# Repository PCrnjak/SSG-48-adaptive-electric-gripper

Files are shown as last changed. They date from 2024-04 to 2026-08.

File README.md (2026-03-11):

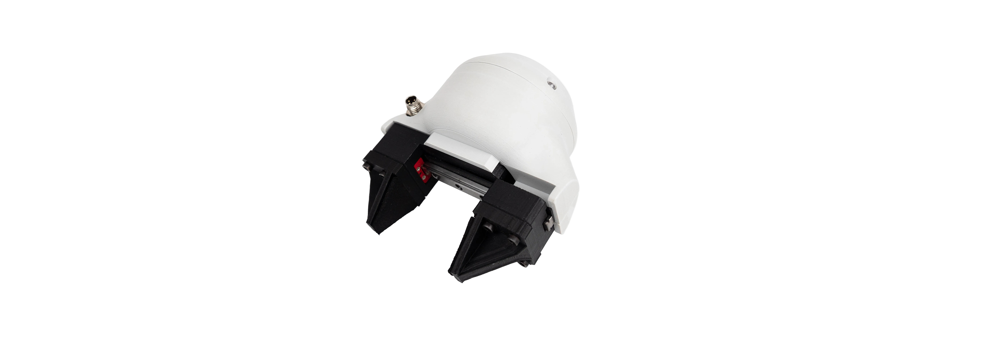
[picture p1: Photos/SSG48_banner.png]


<div align="center">

# SSG48 adaptive electric gripper
        

## [▶️YouTube🔴 Video of Gripper in Action!](https://www.youtube.com/shorts/DQgi8Ua-VAU)

</div>

## 📖 Project Overview

**SSG-48 adaptive electric gripper** is a gripper based on [Spectral micro BLDC drivers](https://source-robotics.com/products/spectral-micro-bldc-controller). It is a gripper capable of controlling its gripping force, making it perfect for assembly tasks and human-robot collaboration. Force can be adjusted from 5 N to 80 N allowing you to grasp a wide range of items; from delicate and soft to rigid and sturdy.

Mechanical files and firmware are open source allowing you to add a custom griping tool and attach it to any robotic arm or robot. Gripper software is also open-source. Gripper has a stroke of 48 mm and a mass of 400g.

## ⚒️How to build / Where to buy?

You can buy SSG48 adaptive electric gripper on our website: https://source-robotics.com/products/compliant-gripper

If you want to Source all the parts yourself and build your own follow these steps:

* Source all the parts from the [BOM](https://github.com/PCrnjak/SSG-48-adaptive-electric-gripper/tree/main/BOM)
* Follow [Assembly instructions](https://github.com/PCrnjak/SSG-48-adaptive-electric-gripper/tree/main/Assembly%20manual) or [Video instructions](https://www.youtube.com/watch?v=127zXHKuqIg) to assemble your gripper
* Follow [DOCS](https://source-robotics.github.io/SSG48-gripper-docs/page1_about_the_gripper/) to get your gripper up and running.

## 📚Documentation:

- [Product website](https://source-robotics.com/products/compliant-gripper)
- [GUI software](https://github.com/PCrnjak/SSG-gripper-GUI) 
- [Building instructions](https://github.com/PCrnjak/SSG-48-adaptive-electric-gripper/tree/main/Assembly%20manual)
- [BOM](https://github.com/PCrnjak/SSG-48-adaptive-electric-gripper/tree/main/BOM)
- [DOCS](https://source-robotics.github.io/SSG48-gripper-docs/page1_about_the_gripper/)
- [Python API](https://github.com/PCrnjak/Spectral-BLDC-Python/tree/main)
- [ROS2 package for SSG48 gripper](https://github.com/Lass6230/ssg48_adaptive_electric_gripper_ros2) /// [ROS2 package for MSG gripper](https://github.com/BiomechatronicsLab/source_robotics_msg_gripper_ros2)
- [URDF & MJCF files](/SSG48_gripper_description/)

## 💻Quick start code example

```python
import Spectral_BLDC as Spectral
import time

Communication1 = Spectral.CanCommunication(bustype='slcan', channel='COM20', bitrate=1000000)
Motor1 = Spectral.SpectralCAN(node_id=0, communication=Communication1)

Motor1.Send_Clear_Error()
Motor1.Send_gripper_calibrate()
time.sleep(4)

temp_var = 0
while True:
   if temp_var == 0:
      Motor1.Send_gripper_data_pack(50,100,700,1,1,0,0) 
      temp_var = 1
   elif temp_var == 1:
      Motor1.Send_gripper_data_pack(240,100,700,1,1,0,0) 
      temp_var = 0

   message, UnpackedMessageID = Communication1.receive_can_messages(timeout=0.2) 

   if message is not None:
      print(f"Message is: {message}")
      print(f"Node ID is : {UnpackedMessageID.node_id}")
      print(f"Message ID is: {UnpackedMessageID.command_id}")
      print(f"Error bit is: {UnpackedMessageID.error_bit}")
      print(f"Timestamp is: {message.timestamp}")

   time.sleep(3)
```

## 🌐 More about the SSG48 Adaptive Electric Gripper

| YouTube | Hackaday | Instagram | Twitter |
|---|---|---|---|
|  |  |  |  |

| Discord | Forum | Blog |
|---|---|---|
|  |  |  |

## ⚠️ Safety, Liability & Disclaimer
This project includes experimental software, hardware designs, and assembly documentation that are still under development and may contain bugs, errors, or incomplete features. By using, building, or modifying this project, you acknowledge that:

* You use this project entirely at your own risk
* You are solely responsible for safe assembly, testing, and operation
* No guarantee is made regarding correctness, safety, or reliability
* The authors are not responsible for any damage, injury, or loss resulting from the use or misuse of this project
* Hardware performance and safety depend on user assembly, component quality, calibration, and handling, which cannot be guaranteed
* This project is provided “as is.” If you choose to build a device yourself using these files, designs, or instructions, you do so without any warranties or guarantees, including regarding safety, reliability, or suitability for any particular purpose.

THIS PROJECT INVOLVES LETHAL VOLTAGES AND OTHER SERIOUS HAZARDS THAT CAN CAUSE SEVERE INJURY. YOU MUST READ THE FULL [SAFETY WARNING AND DISCLAIMER DOCUMENT](SAFETY_WARNING_AND_DISCLAIMER.md)  BEFORE USING ANY PROJECT FILES. BY PROCEEDING, YOU ACKNOWLEDGE AND ACCEPT ALL RISKS AND AGREE TO USE THIS PROJECT ENTIRELY AT YOUR OWN RESPONSIBILITY.

## 💸Support the project

The majority of this project is open source and freely available to everyone. Your assistance, whether through donations or advice, is highly valued. Thank you!

 


## 🛡️ Licensing
Project is under Apache 2.0 Licence

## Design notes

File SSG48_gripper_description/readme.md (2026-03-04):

# Source Robotics SSG48 gripper Description (MJCF)

> [!IMPORTANT]
> Requires MuJoCo 3.1.3 or later.

## Changelog

See [CHANGELOG.md](./CHANGELOG.md) for a full history of changes.

## ⚒️TODO 

- Add correct joint limits to URDF and MJCF files

## Overview

This package contains a simplified robot description (MJCF) and URDF files of the [SSG48 gripper](https://source-robotics.com/products/compliant-gripper) developed by [Source Robotics](https://source-robotics.com/).

## Jaw options

Folder contains few different jaw options for the gripper. You can change them by replacing the existing jaw options in the mesh folder by the ones you want.

## Online mujoco viewer

https://mujoco-viewer.org/

## URDF folder

[URDF](./URDF/) folder contains:
* SSG48 gripper
* Jaw options folder

More about URDF here: [Link](./urdf.md)

## URDF → MJCF derivation steps

1. Loaded the URDF into MuJoCo and saved a corresponding MJCF.
2. Manually edited the MJCF to extract common properties into the `<default>` section.
3. Added position-controlled actuators for the arm.
4. Added `scene.xml` which includes the robot, with a textured groundplane, skybox, and haze.

## License

This model is released under an [Apache-2.0 License](LICENSE).

## References

Mjcf reference Mujoco managerie
- references: 
- https://mujoco.readthedocs.io/en/stable/XMLreference.html
- https://github.com/google-deepmind/mujoco_menagerie/tree/main/ufactory_lite6
- https://github.com/google-deepmind/mujoco_menagerie/blob/main/trossen_vx300s/vx300s.xml 
- https://github.com/google-deepmind/mujoco_menagerie/blob/main/aloha/aloha.xml
- https://github.com/google-deepmind/mujoco_menagerie/blob/main/franka_emika_panda/panda.xml 
- https://github.com/jeongeun980906/lerobot-mujoco-tutorial/blob/master/asset/robotis_omy/omy.xml

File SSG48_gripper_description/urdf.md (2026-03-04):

Free online URDF viewers:
- https://gkjohnson.github.io/urdf-loaders/javascript/example/bundle/
- https://urdf.d-robotics.cc/
- https://viewer.robotsfan.com/

TO view any of the URDF arms drag the folder into the online viewer.

---

Great guide on how to generate URDF in solidworks: [Link](https://www.youtube.com/watch?v=I08lO_SRBbk)

---

How to convert URDF to MUJOCO file format: [Link](https://www.youtube.com/watch?v=v2OfmQaoIH4) 

Note add .\ before compile command on windows

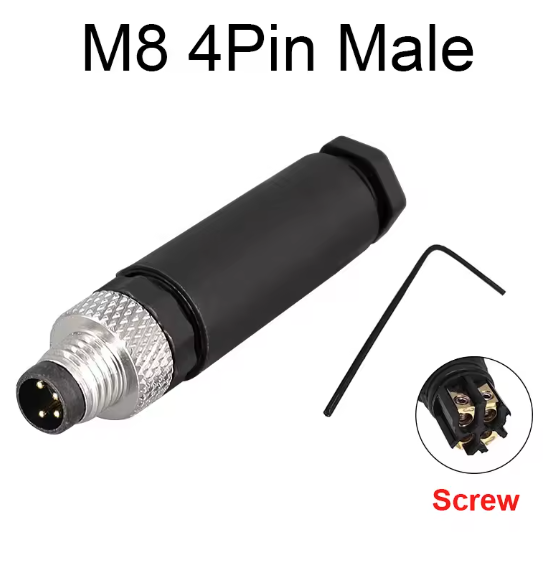
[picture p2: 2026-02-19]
Photos/M8 male.png

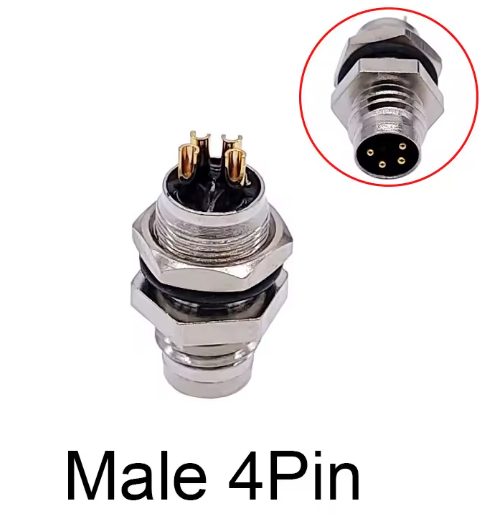
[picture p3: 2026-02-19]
Photos/M8connectormale4pin.png

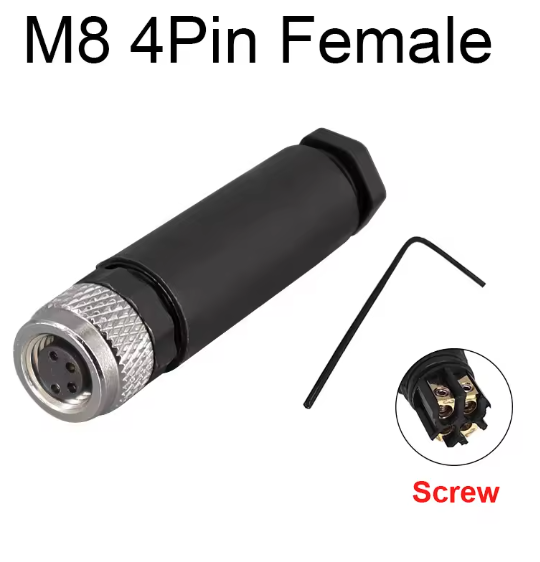
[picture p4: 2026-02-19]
Photos/M8_female.png

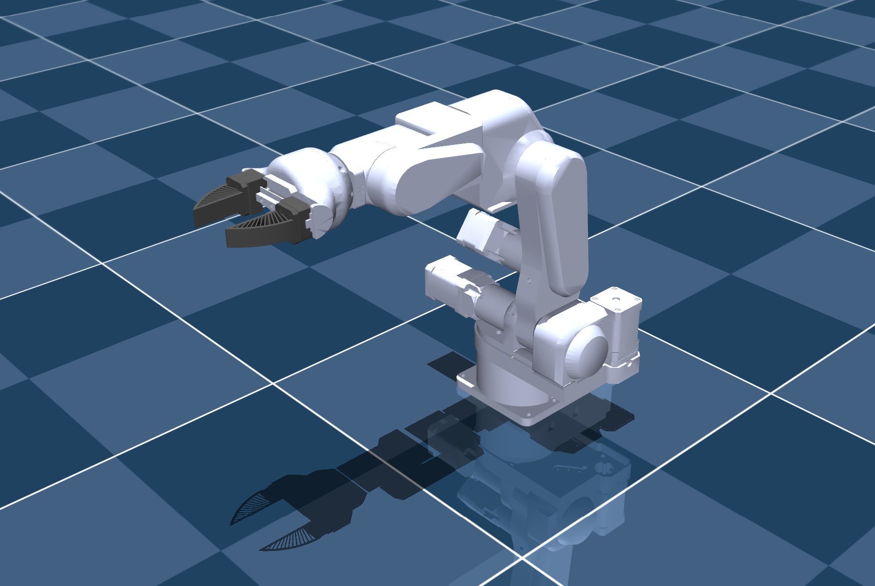
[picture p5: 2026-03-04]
SSG48_gripper_description/PAR6_SSG48_img.png

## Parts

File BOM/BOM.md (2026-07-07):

# Gripper – Bill of Materials (BOM)

This BOM lists all components required to build the SSG48 gripper. Quantities are for **one gripper**.

> [!NOTE]
> If any product links are broken, unavailable, or no longer point to the correct item, please [open an issue](https://github.com/PCrnjak/SSG-48-adaptive-electric-gripper/issues/new), send us a message on Discord, or contact us via email. You can also use the reference images to find the same or an equivalent part from another supplier.

---

## Screws and Nuts

| Diameter / Type | Length | Quantity | Description | Link |
|---|---|---|---|---|
| M2.5 | 8 mm | 4 |  |  |
| M2 | 4 mm | 8 |  |  |
| M3 | 5 mm | 5 | Cheese head screw |  |
| M2 | 10 mm | 1 |  |  |
| M3 | 8 mm | 7 | Cheese head screw |  |
| M4 | 10 mm | 4 |  |  |
| M3 | 12 mm | 4 |  |  |
| M3 | 10 mm | 4 |  |  |
| M2 | 10 mm | 3 |  |  |

---

## Brass Inserts

| Thread | Length | Outer Diameter | Quantity | Link |
|---|---|---|---|---|
| M3 | 3 mm | 4.5 mm | 1 | [Link](https://s.click.aliexpress.com/e/_DnCPrW9) |
| M3 | 5 mm | 4.5 mm | 15 | [Link](https://s.click.aliexpress.com/e/_DnCPrW9) |

---

## Motors

> [!NOTE]
>     **If you are having a hard time sourcing motors consider building our [MSG gripper](https://github.com/Source-Robotics/MSG-compliant-AI-stepper-gripper)!**

| Type | Quantity | Description | Link |
|---|---|---|---|
| GBM5208-75 | 1 |  | [Link](https://s.click.aliexpress.com/e/_DmkWskt) //  [Alibaba link](https://www.alibaba.com/product-detail/Flashhobby-GBM5208-75-0-3KG-5208_1601005642241.html) |

---

## Mechanical Components

| Type | Quantity | Description | Link |
|---|---|---|---|
| Shaft coupler | 1 | 8 mm hole shaft, M4 screw holes | [Link](https://www.aliexpress.com/item/4000208248034.html?spm=a2g0o.order_list.order_list_main.521.6af018026rwEsK) |
| MGN7C slider | 2 |  | [Link](https://s.click.aliexpress.com/e/_oEZfs3x) |
| Linear guide | 1 | 100 mm | [Link](https://s.click.aliexpress.com/e/_oBSDfjN) |
| Magnet | 1 | 6 mm diameter, 2.5 mm thickness |  |

---

## Electronics

| Type | Quantity | Description | Link |
|---|---|---|---|
| Spectral micro BLDC driver | 1 | [source-robotics.com](http://source-robotics.com/) | [Link](https://source-robotics.com/products/spectral-micro-bldc-controller) |
| XH 2.54 mm, 300 mm, 2P, double-ended | 1 | Cable for 24 V | [Link](https://s.click.aliexpress.com/e/_c4XKzTj9) |
| ZH 1.5 mm, 300 mm, 2P, double-ended | 1 | Cable for CAN bus | [Link](https://s.click.aliexpress.com/e/_c4XKzTj9) |
| Male 4-pin connector | 1 | [Reference image](../Photos/M8connectormale4pin.png) | [Link](https://s.click.aliexpress.com/e/_DCG5Rff) |

---

## Cables

Parts for the DIY cable version below:

| Type | Length / Spec | Quantity | Description | Link |
|---|---|---|---|---|
| 26 AWG cable | 0.15 mm², 4-wire twisted pair | 0.4 m | Usually 35 cm cable is enough | [Link](https://s.click.aliexpress.com/e/_DeGUD4Z) |
| M8 4-pin male wire connector | — | 1 | [See reference image](../Photos/M8_male.png) | [Link](https://s.click.aliexpress.com/e/_DCG5Rff) |
| M8 4-pin female wire connector | — | 1 | [See reference image](../Photos/M8_female.png) | [Link](https://s.click.aliexpress.com/e/_DCG5Rff) |

Check out the cable building guide [here](../Assembly%20manual/Building_cables.md)

---

> **Note:** Equivalent parts from other suppliers may be used as long as specifications match.

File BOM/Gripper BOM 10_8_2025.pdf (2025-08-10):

Screws and nuts:
diameter , length | quantity | Description | Link
M2.5 x 8mm | 4
M2 x 4mm | 8
M3 x 5mm cheese head | 5
M2 x 10 mm | 1
M3 x 8mm cheese head | 7
M4 x 10mm | 4
M3 x 12 mm | 4
M3 x 10 mm | 4
M2 x 10 mm | 3
Brass inserts:
Length 3mm, M3 (OD 4.5mm) | 1 | | Link (https://s.click.aliexpress.com/e/_DnCPrW9)
Length 5mm, M3 (OD 4.5mm) | 15 | | Link (https://s.click.aliexpress.com/e/_DnCPrW9)
Motors:
Type | quantity | Description | Link
GBM5208-75 | 1 | Link (https://s.click.aliexpress.com/e/_DmkWskt) | Link (https://s.click.aliexpress.com/e/_DmkWskt)
Mechanical:
Type | quantity | Description | Link
Shaft coupler | 1 | 8 mm hole shaft, M4 screw holes | Link (https://www.aliexpress.com/item/4000208248034.html)
MGN7C slider | 2 | | Link (https://s.click.aliexpress.com/e/_oEZfs3x)
Linear guide | 1 | 100mm | Link (https://s.click.aliexpress.com/e/_oBSDfjN)
Magnet | 1 | 6 mm diameter, 2.5 mm tickness
Electronics:
Type | quantity | Description | Link
Spectral micro BLDC driver | 1 | source-robotics.com | Link (https://source-robotics.com/products/spectral-micro-bldc-controller)
XH 2.54MM, 300MM, 2P, Double end same | 1 | Cable for 24V | Link (https://s.click.aliexpress.com/e/_DFlNuNJ)
ZH 1.5MM, 300MM, 2P, Double end same | 1 | Cable for CAN bus | Link (https://s.click.aliexpress.com/e/_DFlNuNJ)
Male 4pin connector | 1 | | Link (https://s.click.aliexpress.com/e/_DCG5Rff)
Cable:
26AWG 0.15mm2 4wire twisted pair | 0.4 meter | Usually 35 cm cable is enough | Link (https://s.click.aliexpress.com/e/_DeGUD4Z)

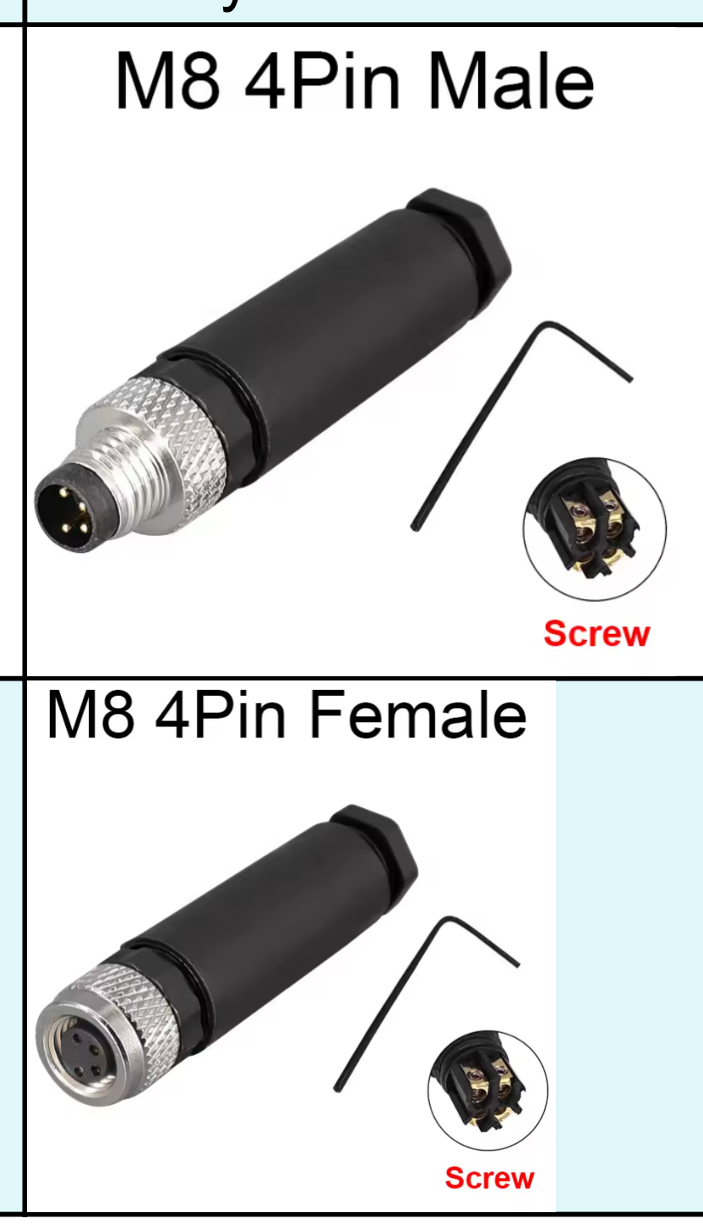
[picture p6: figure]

4 pin male wire connector | 1 | | Link (https://s.click.aliexpress.com/e/_DCG5Rff)
4 pin female wire connector | 1 | | Link (https://s.click.aliexpress.com/e/_DCG5Rff)

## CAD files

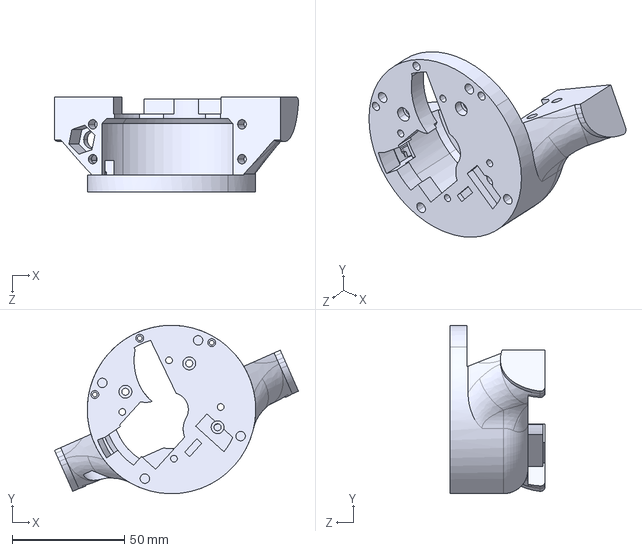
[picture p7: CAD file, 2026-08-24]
STEPS/Gripper STEP files/mirror_main_body.STEP
108.6 x 75.0 x 42.3 mm

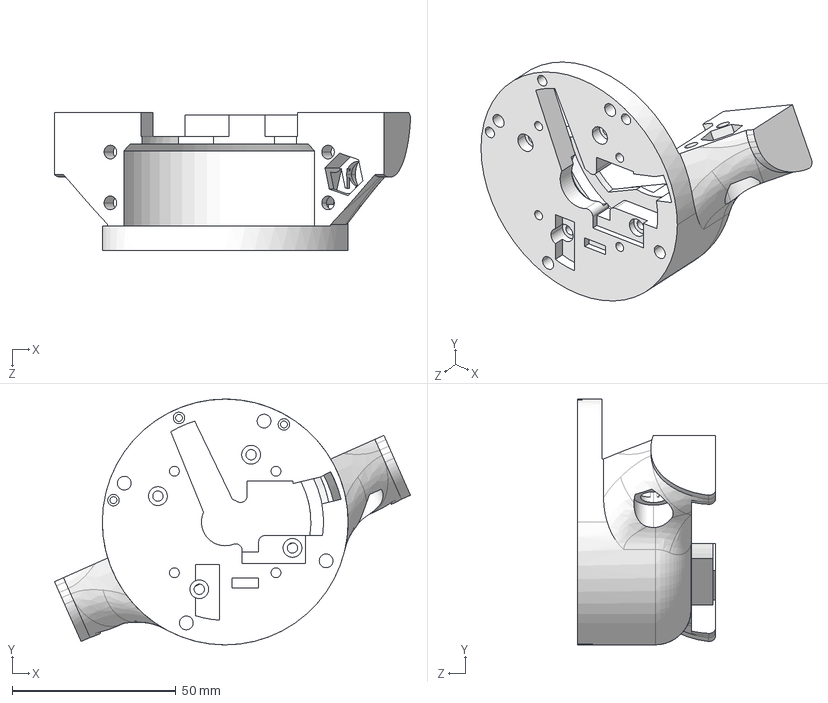
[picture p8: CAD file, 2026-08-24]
STEPS/Gripper STEP files/main_body.STEP
108.6 x 75.0 x 42.3 mm

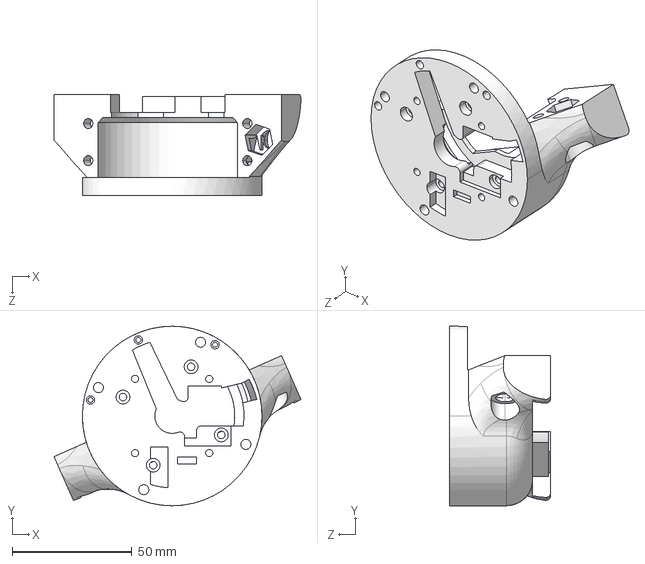
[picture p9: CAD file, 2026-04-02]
STEPS/Gripper STEP files/mainbody_large_bearing_version.STEP
103.2 x 75.0 x 42.3 mm

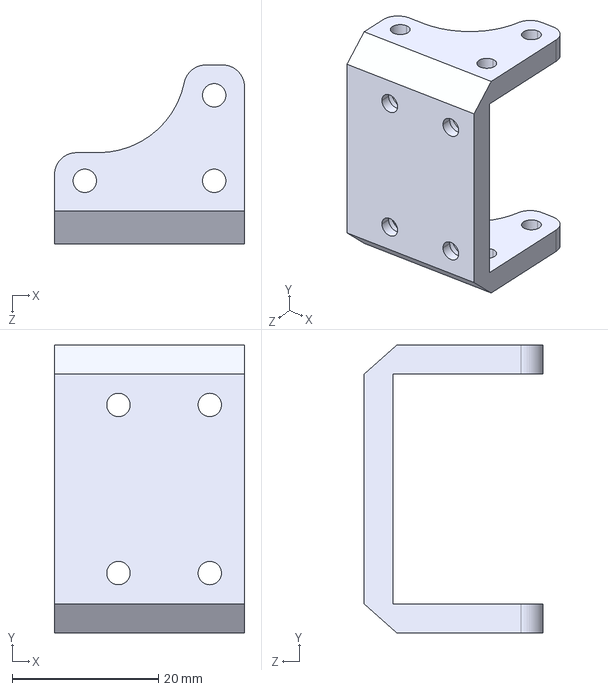
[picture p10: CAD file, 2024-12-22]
gripper jaws/Jaw_plate_fin_ray.STEP
26.0 x 39.4 x 24.5 mm

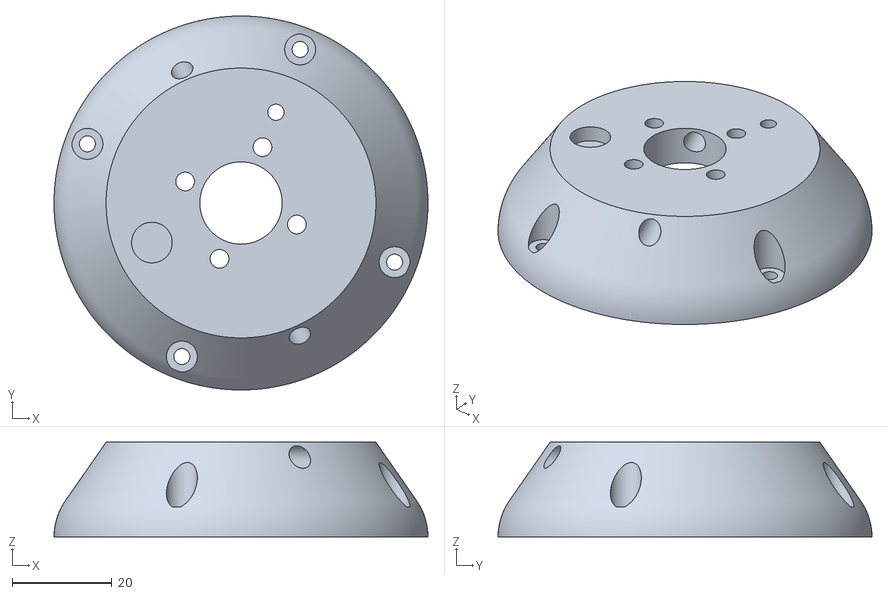
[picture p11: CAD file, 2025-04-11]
Gripper STL parts/coupler_connector_PAR6.STL
75.0 x 75.0 x 19.0

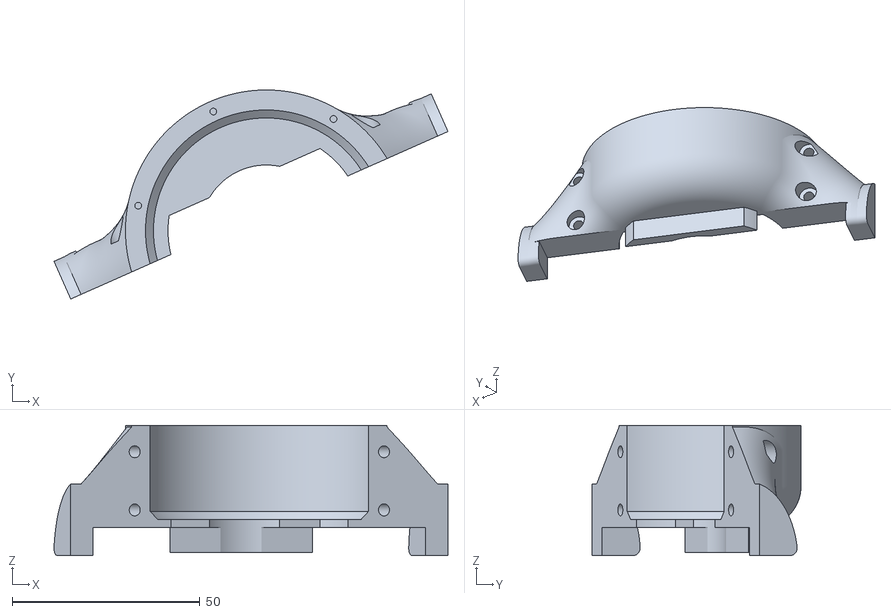
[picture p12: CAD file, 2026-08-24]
Gripper STL parts/V2/Lid_large_bearing.STL
105.0 x 55.7 x 34.6

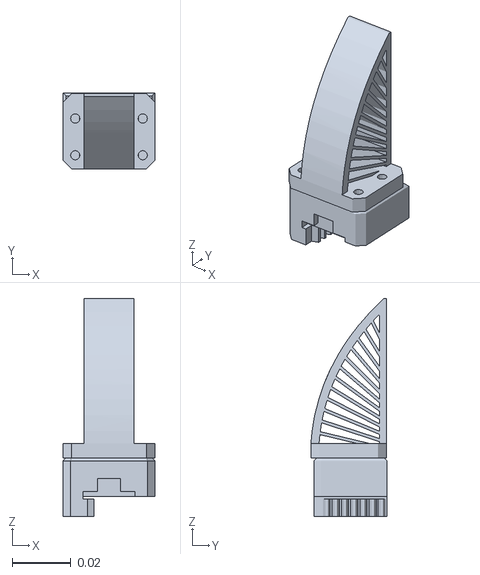
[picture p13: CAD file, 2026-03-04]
SSG48_gripper_description/assets/jaw1_SSG48.STL
0.0314 x 0.026 x 0.0743

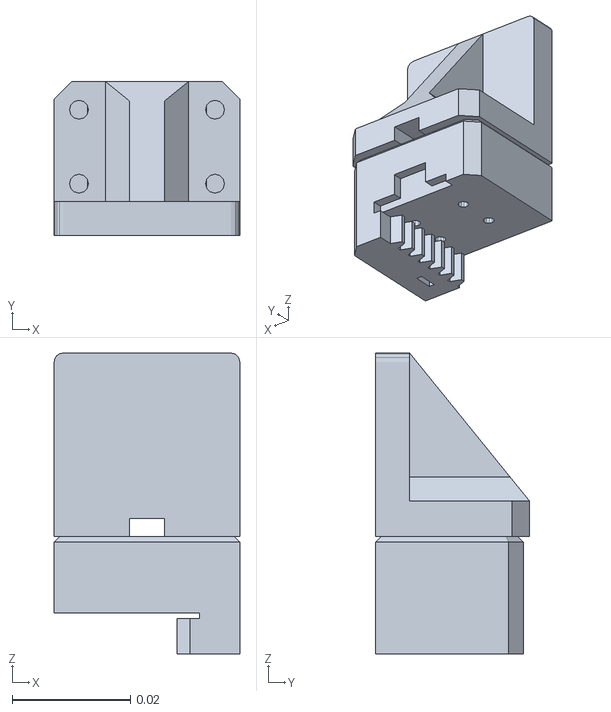
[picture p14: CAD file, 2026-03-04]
SSG48_gripper_description/assets/SSG48 gripper jaws/Solid_jaws/jaw2.STL
0.0314 x 0.026 x 0.0509

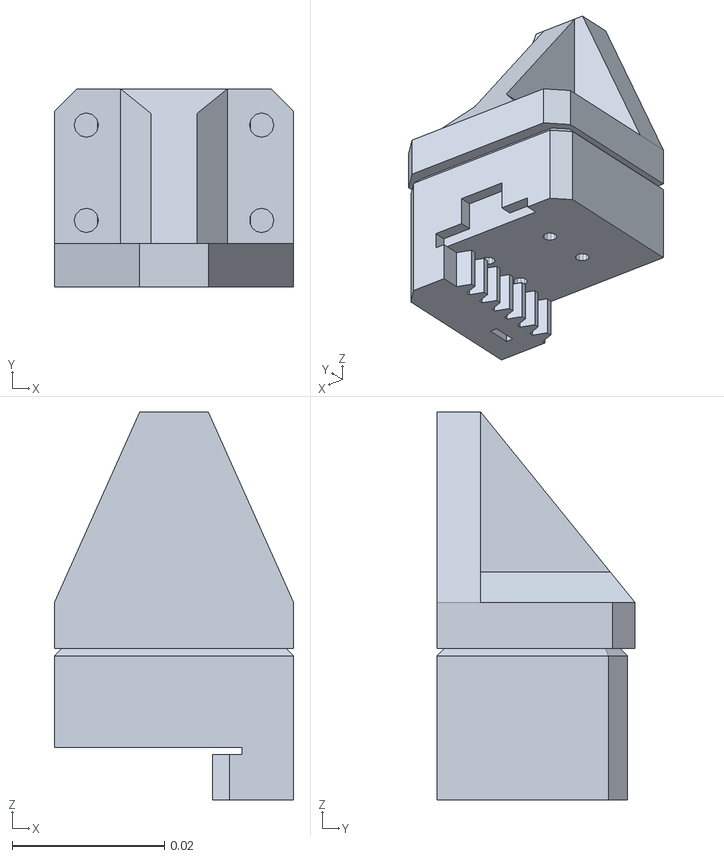
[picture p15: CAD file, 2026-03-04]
SSG48_gripper_description/assets/SSG48 gripper jaws/solid_jaws_pinch/jaw2.STL
0.0314 x 0.026 x 0.0509

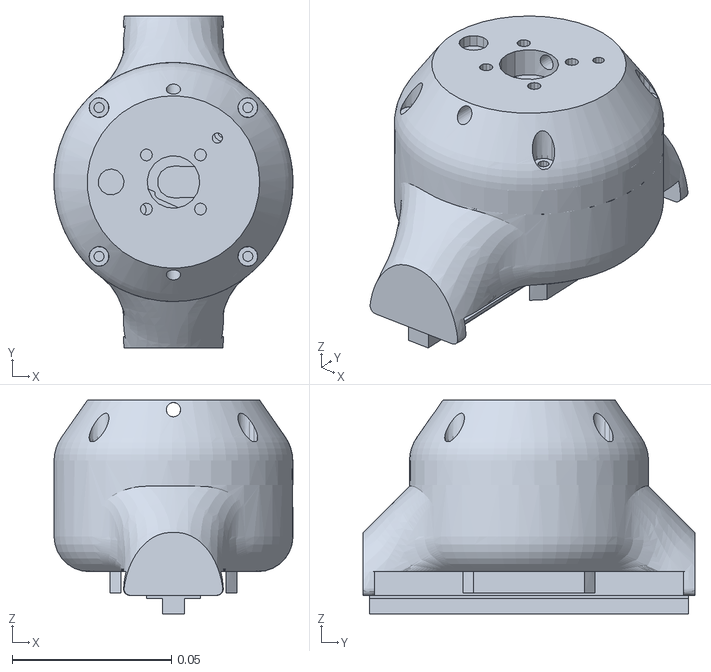
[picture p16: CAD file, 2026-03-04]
SSG48_gripper_description/URDF/ssg48_gripper/meshes/gripper.STL
0.075 x 0.104 x 0.0671

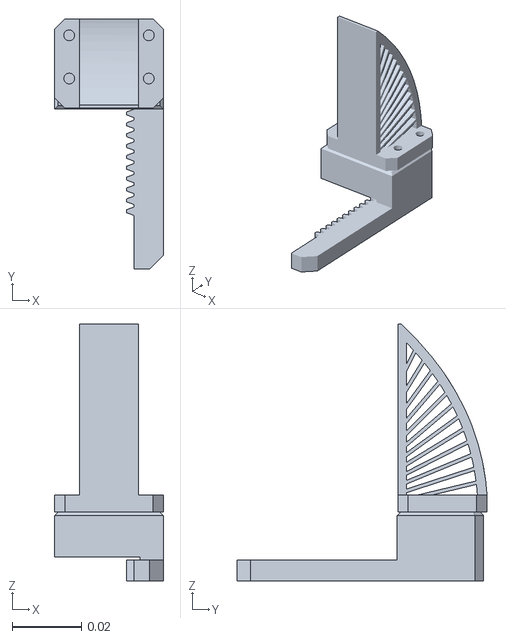
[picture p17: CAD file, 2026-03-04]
SSG48_gripper_description/URDF/ssg48_gripper/ssg48_JAW_OPTIONS/FIN_ray_jaws/jaw2.STL
0.0314 x 0.0723 x 0.0743

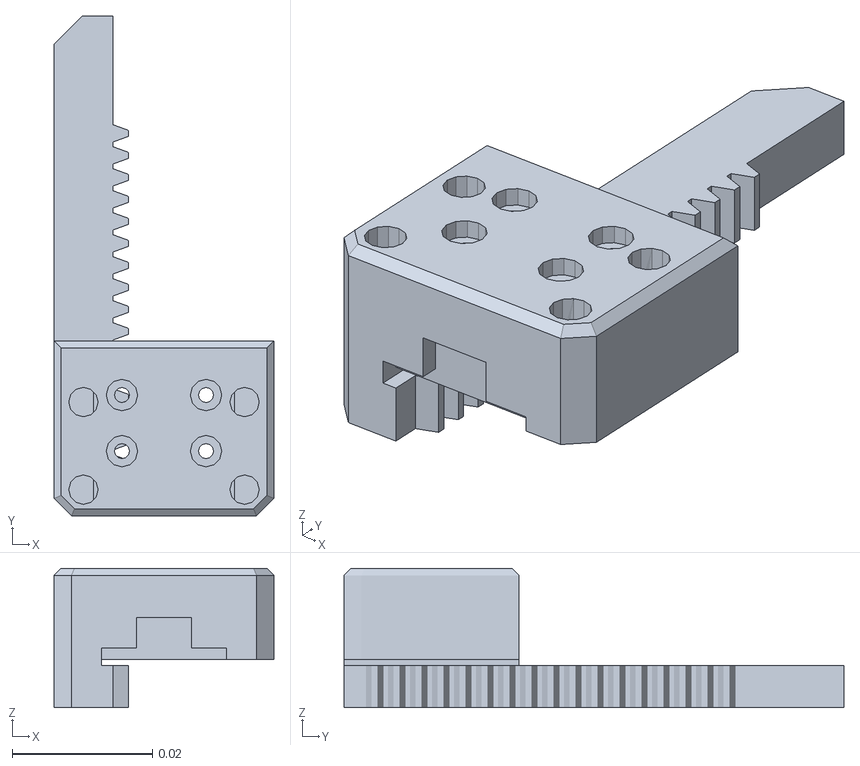
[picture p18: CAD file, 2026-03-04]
SSG48_gripper_description/URDF/ssg48_gripper/ssg48_JAW_OPTIONS/No jaws/jaw2.STL
0.0314 x 0.0713 x 0.0199

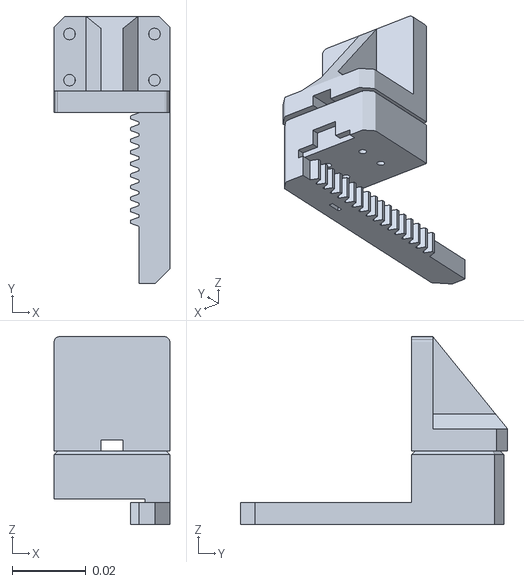
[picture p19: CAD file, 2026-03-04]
SSG48_gripper_description/URDF/ssg48_gripper/ssg48_JAW_OPTIONS/solid_jaws/jaw2.STL
0.0314 x 0.0723 x 0.0509

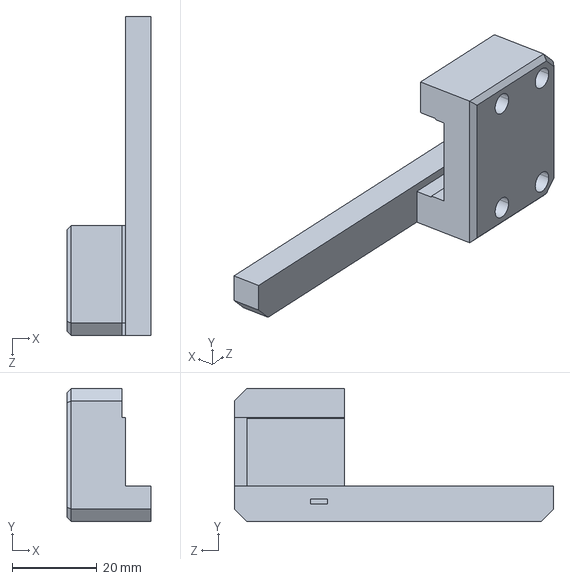
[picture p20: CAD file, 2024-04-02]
STEPS/3D MODEL/JAW.STEP
19.9 x 31.4 x 75.3 mm

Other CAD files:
SSG48_gripper_description/assets/SSG48 gripper jaws/Fin_ray_jaws/jaw2.STL
SSG48_gripper_description/URDF/ssg48_gripper/ssg48_JAW_OPTIONS/solid_jaws_pinch/jaw1.STL
STEPS/solid_jaws_pinch_foam.STEP
STEPS/UR5 adapter plate/UR_coupler_gripper.STEP
Gripper STL parts/V1/Guide_cover.STL
Gripper STL parts/V1/Magnet_shaft.STL
Gripper STL parts/V1/Main_body_lid.STL
Gripper STL parts/V1/gripper_gear.STL
Gripper STL parts/V1/gripper_jaw.STL
Gripper STL parts/V1/mainbody_mirror_version.STL
Gripper STL parts/V2/Guide_cover.STL
Gripper STL parts/V2/gripper_gear_large_bearing_motor.STL
Gripper STL parts/V2/gripper_jaw.STL
Gripper STL parts/V2/magnet_shaft_large_bearing.STL
SSG48_gripper_description/URDF/ssg48_gripper/meshes/jaw1.STL
SSG48_gripper_description/URDF/ssg48_gripper/ssg48_JAW_OPTIONS/FIN_ray_jaws/jaw1.STL
SSG48_gripper_description/URDF/ssg48_gripper/ssg48_JAW_OPTIONS/No jaws/jaw1.STL
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

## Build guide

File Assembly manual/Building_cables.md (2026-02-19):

## MSG & SSG48 gripper cable

Buy Official cables from Source Robotics: [Link](https://source-robotics.com/)

Parts needed if DIY your own cable:

| Type | Length / Spec | Quantity | Description | Link |
|---|---|---|---|---|
| 26 AWG cable | 0.15 mm², 4-wire twisted pair | 0.4 m | ~40 cm usually sufficient | [Link](https://s.click.aliexpress.com/e/_c4m3ggwn) |
| M8 4-pin male wire connector | — | 1 | [See reference image](../Photos/M8%20male.png) |[Link](https://s.click.aliexpress.com/e/_c4OWHPKF) |
| M8 4-pin female wire connector | — | 1 | [See reference image](../Photos/M8_female.png) | [Link](https://s.click.aliexpress.com/e/_c4OWHPKF) |

> [!NOTE]
>     **PAROL6 and PAR6 use different cables for SSG48 and MSG grippers. Using incorrect one can damage your robot**

## Wire diagram for PAROL6 robotic arm

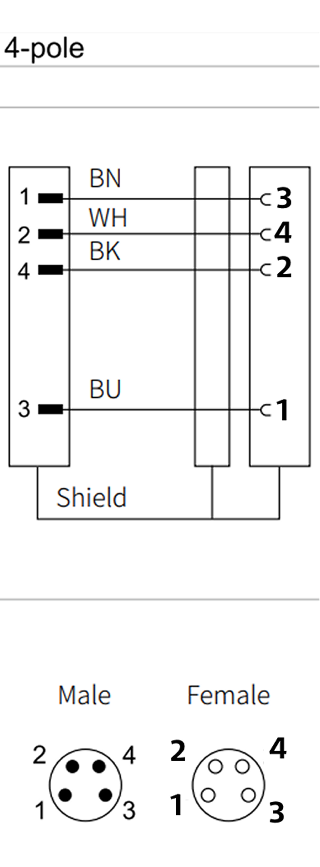
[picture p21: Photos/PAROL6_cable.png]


## Wire diagram for PAR6 robotic arm
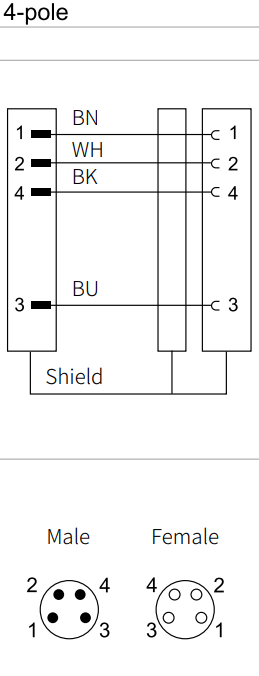
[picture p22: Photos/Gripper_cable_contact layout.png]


## Final look of the cable 

End result of this cable assembly needs to look like this:

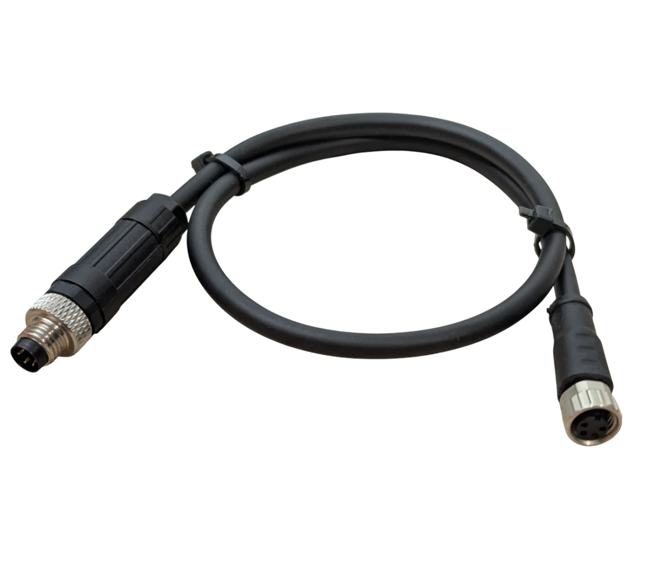
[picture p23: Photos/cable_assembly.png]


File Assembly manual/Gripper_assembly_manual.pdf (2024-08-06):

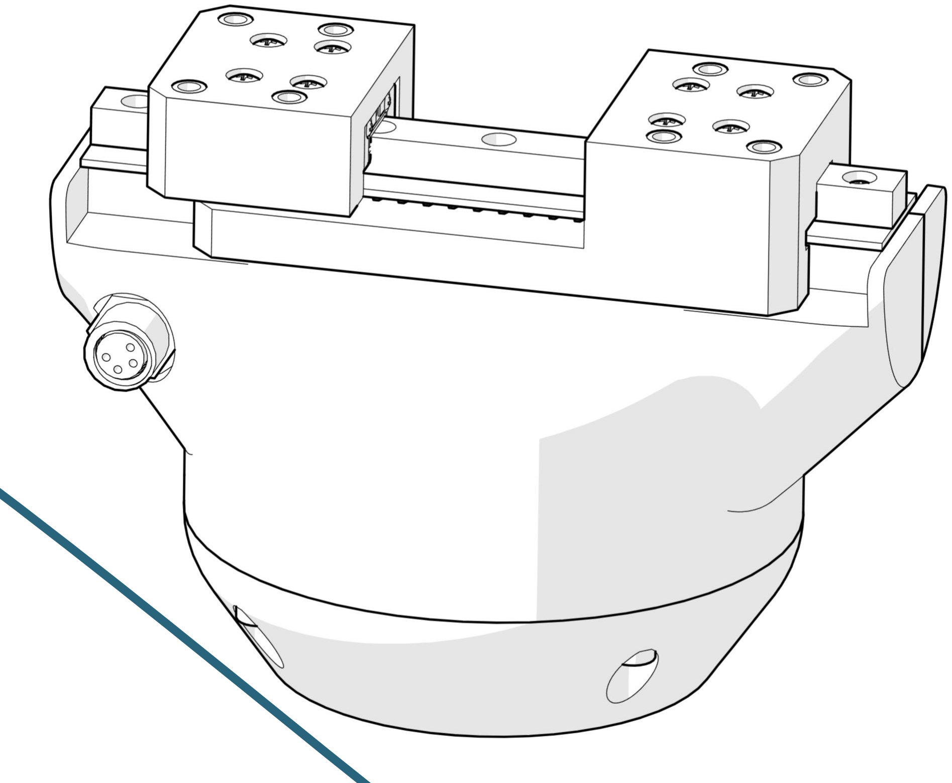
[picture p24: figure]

# SSG-48 Adaptive gripper assembly manual

Version 1.1, rev1, date 2.21.2024

Disclaimer important notice

The SSG-48 adaptive electric gripper and its associated part are specifically intended for engineering development, demonstration, or evaluation purposes. They are not considered to be a final product suitable for general consumer use. Individuals handling these products must have proper electronics and robotics training and adhere to good engineering practices. It should be noted that these goods may not fulfill all the required design, marketing, and manufacturing-related protective measures, including product safety and environmental considerations typically found in finished products. The SSG-48 adaptive electric gripper is not compliant with the European Union directives concerning electromagnetic compatibility, restricted substances (RoHS), recycling (WEEE), FCC, CE, or UL. Consequently, it may not meet the technical requirements outlined in these directives or other related directives.

The user assumes full responsibility and liability for the correct and safe handling of the robot. Additionally, the user agrees to indemnify the Source Robotics team against any claims arising from the use or handling of the products. Given the open construction of the product, it is the user's responsibility to take all necessary precautions.

EXCEPT FOR THE INDEMNITY DESCRIBED ABOVE, NEITHER PARTY SHALL BE HELD LIABLE TO THE OTHER FOR ANY INDIRECT, SPECIAL, INCIDENTAL, OR CONSEQUENTIAL DAMAGES.

Disclaimer important notice

Before building this gripper please read the whole manual! This machine can cause harm to you and people around you. It can burn, electrocute and physically hurt you if you are not careful. Please read these instructions carefully!

Assembly manual

Welcome to the SSG-48 adaptive electric gripper assembly manual. SSG-48 adaptive electric gripper is a gripper based on Spectral micro BLDC drivers. It is a gripper capable of controlling its gripping force, making it perfect for assembly tasks and human-robot collaboration.
It is made by Source Robotics, designed by Petar Crnjak

All additional information can be found here:
- | Github project repository - | most up to date BOM, parts, docs, manuals… (https://github.com/PCrnjak/SSG-48-adaptive-electric-gripper)
- Docs page - latest documentation on PAROL software (https://source-robotics.github.io/SSG48-gripper-docs/page1_about_the_gripper/)
- | Official product page - | Source robotics (https://source-robotics.com/products/compliant-gripper)

You can also ask help and advice from community:
- | Official discord server: | link (https://discord.gg/prjUvjmGpZ)
- | Or send us an email at: | info@source-robotics.com

And you can follow us on social media:

Assembly manual

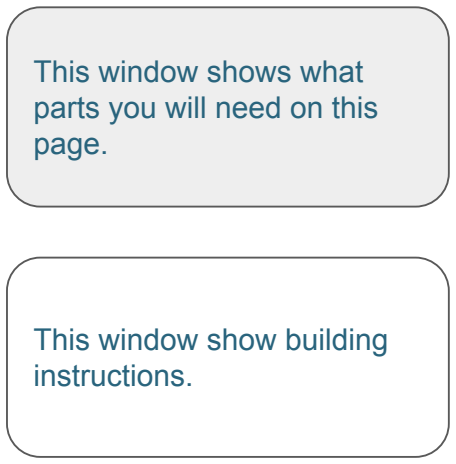
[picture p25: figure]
This window shows what parts you will need on this page.; This window show building instructions.

All screws shown are same size and only for reference. For correct size read the instructions stated on the page what screw to use.

This document only shows assembly manual, all other files like BOM, printing table, STL files can be found on GitHub page of the project.

All parts should be printed with PETG material. Reference printing table for optimal infills and printing settings.

Wires are not shown but detailed instructions are given on how to route the wires.

Assembly manual - Print preparation

Some parts need to be printed with support. Before using those parts make sure to clean all support material.

Printer settings we used:
- Printer: Prusa MK2S
- Material: PETG
- Layer height:
- Support: Reference printing table
- Infill: Reference printing table

Assembly manual - Needed tools

Tools you will need to assemble this robot:
- Screwdriver set
- Drill
- Soldering iron
- Imbus wrench (Allen key / HEX key) set
- Torque screwdriver
- Rubber hammer
- Hammer
- Pliers

For screwing we recommend using an electric screwdriver and then precision torque screwdriver or last few turns by hand. If you use drill or electric screwdriver for all the parts you risk destroying your threads.

Assembly manual - Needed consumable items

- Blue threadlocker
- Lithium grease
- Solder
- Heat shrink tube

# Gripper assembly

## Video assembly manual can be found here: https://www.youtube.com/watch?v=127zXHKuqIg

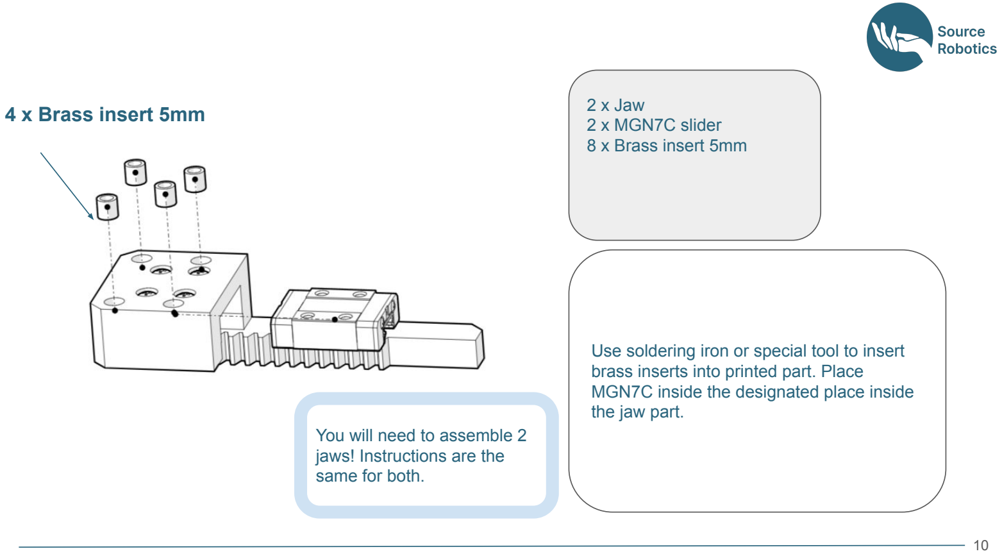
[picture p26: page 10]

2 x Jaw
2 x MGN7C slider
8 x Brass insert 5mm

Use soldering iron or special tool to insert brass inserts into printed part. Place
MGN7C inside the designated place inside the jaw part.

### 4 x Brass insert 5mm

You will need to assemble 2 jaws! Instructions are the same for both.

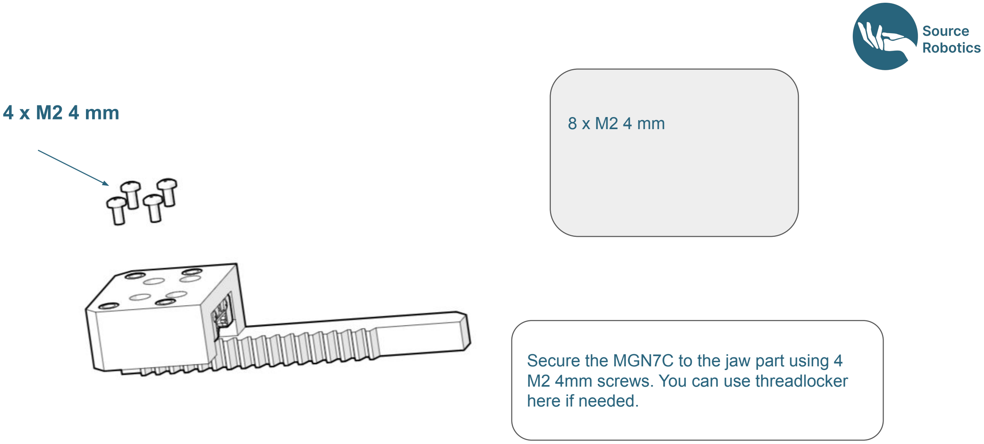
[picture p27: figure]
M2 4mm screws. You can use threadlocker here if needed.

Secure the MGN7C to the jaw part using 4

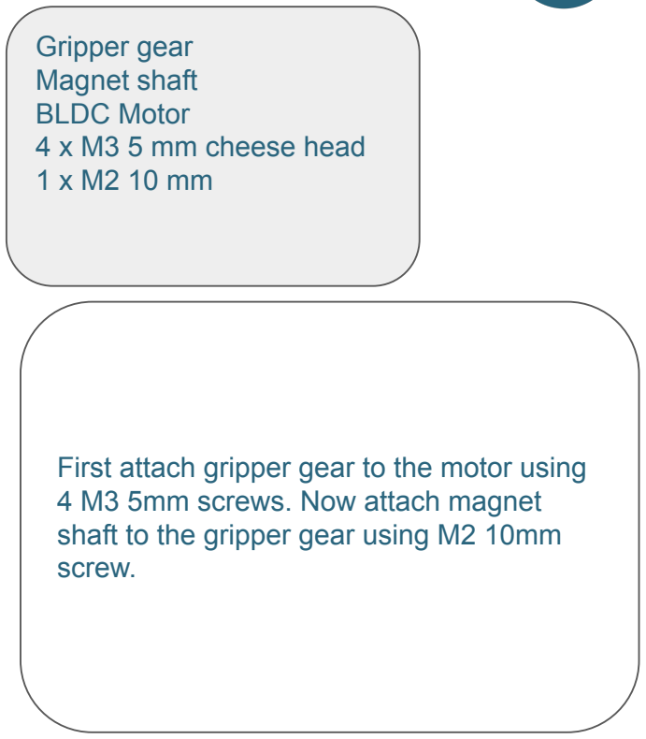
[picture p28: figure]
Gripper gear Magnet shaft BLDC Motor 4 x M3 5 mm cheese head 1 x M2 10 mm; 4 M3 5mm screws. Now attach magnet shaft to the gripper gear using M2 10mm screw.

First attach gripper gear to the motor using

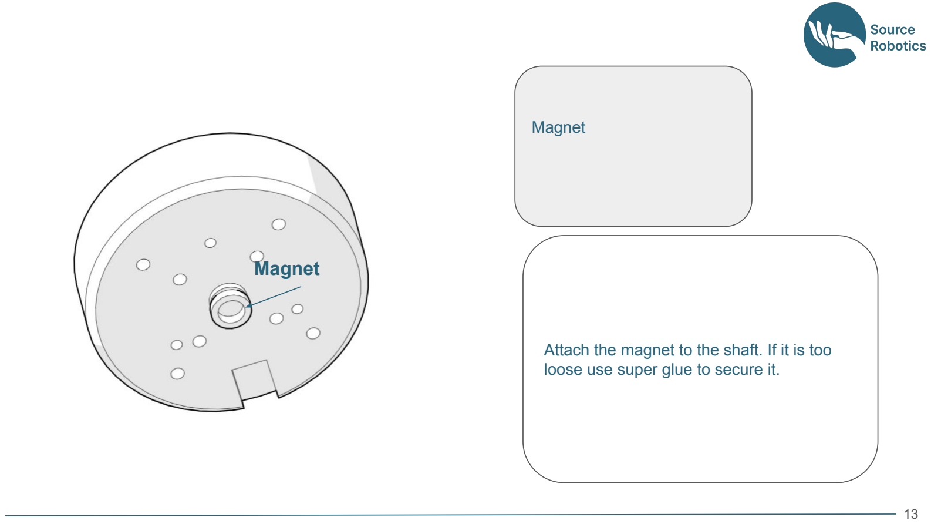
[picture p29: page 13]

Magnet

Attach the magnet to the shaft. If it is too loose use super glue to secure it.

Magnet

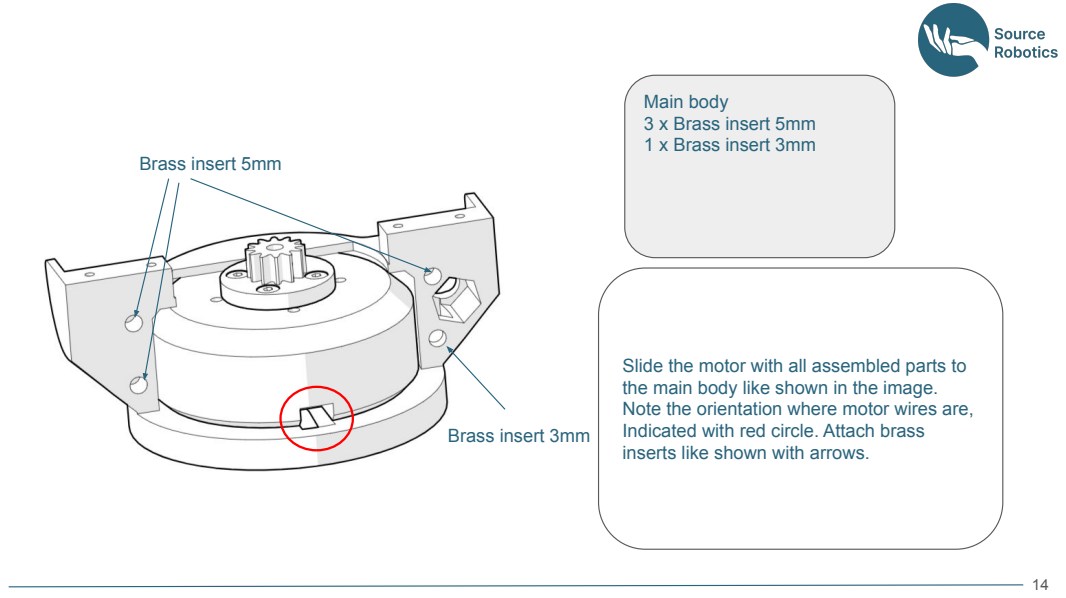
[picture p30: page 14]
Main body 3 x Brass insert 5mm 1 x Brass insert 3mm; Brass insert 3mm; Brass insert 5mm

Slide the motor with all assembled parts to
the main body like shown in the image.
Note the orientation where motor wires are,
Indicated with red circle. Attach brass
inserts like shown with arrows.

market with red cross are not needed. That

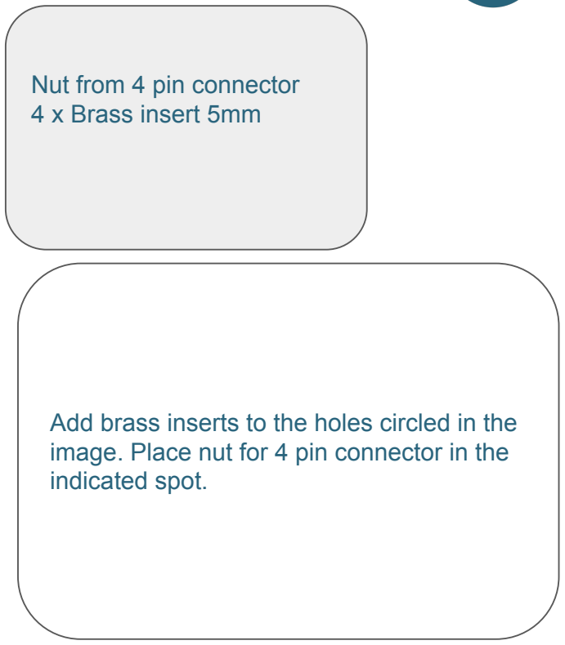
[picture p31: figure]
Nut from 4 pin connector 4 x Brass insert 5mm; indicated spot.
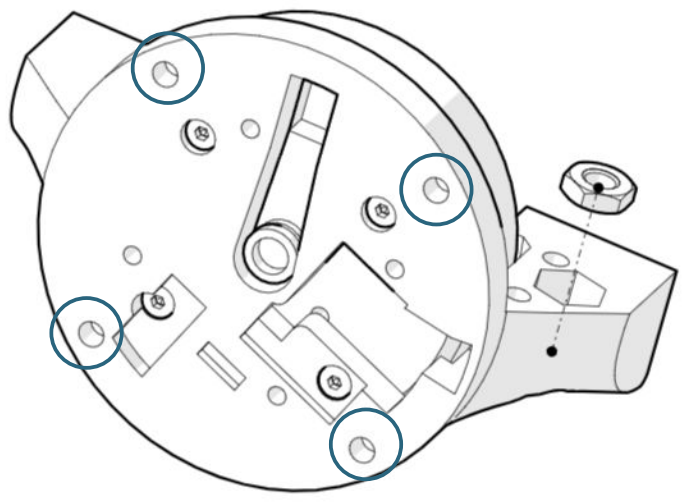
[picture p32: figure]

Add brass inserts to the holes circled in the image. Place nut for 4 pin connector in the

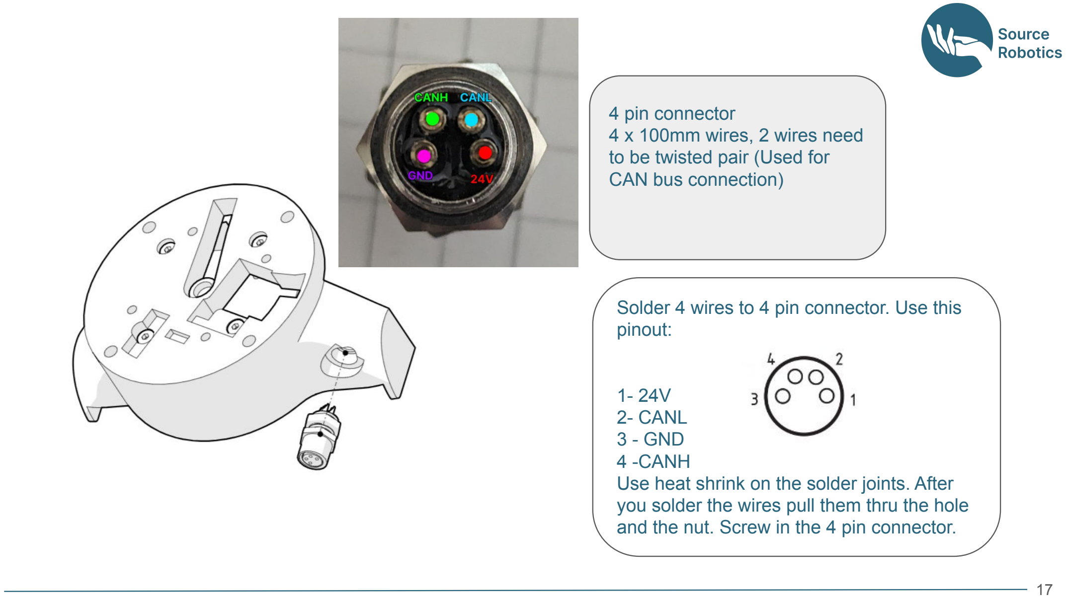
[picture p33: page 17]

4 pin connector
4 x 100mm wires, 2 wires need to be twisted pair (Used for CAN bus connection)

Solder 4 wires to 4 pin connector. Use this pinout:

1- 24V
2- CANL
3 - GND
4 -CANH
Use heat shrink on the solder joints. After you solder the wires pull them thru the hole and the nut. Screw in the 4 pin connector.

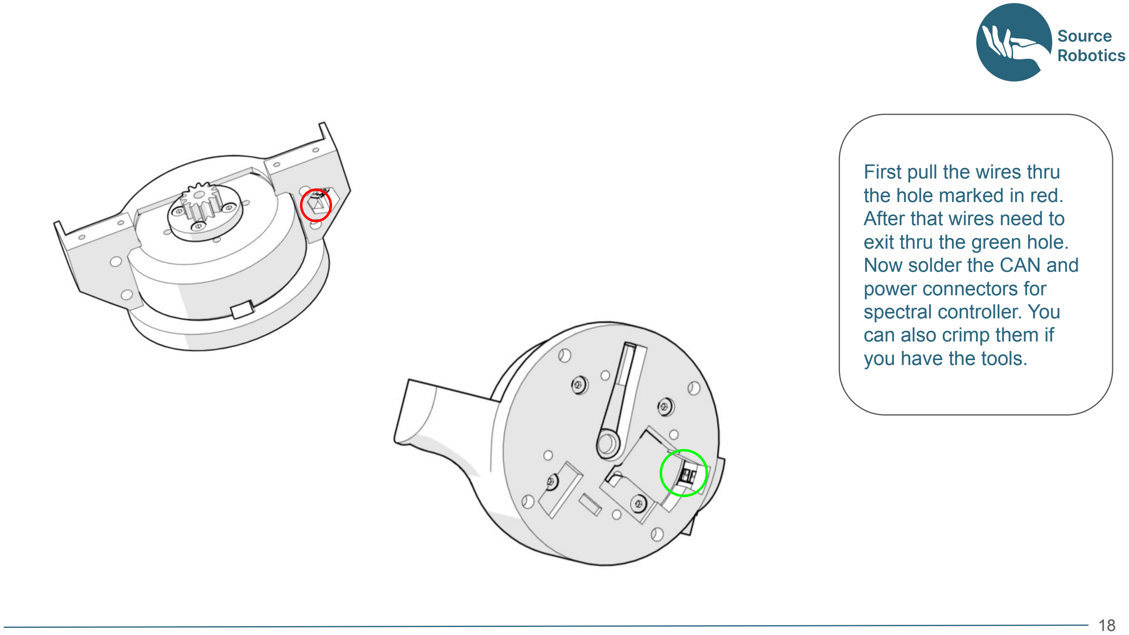
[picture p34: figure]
First pull the wires thru the hole marked in red. After that wires need to exit thru the green hole. Now solder the CAN and power connectors for spectral controller. You can also crimp them if you have the tools.

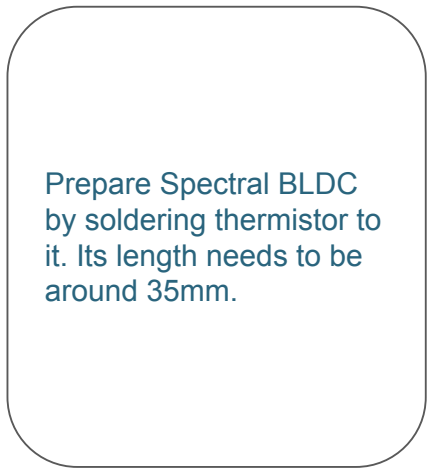
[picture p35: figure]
Prepare Spectral BLDC by soldering thermistor to it. Its length needs to be around 35mm.

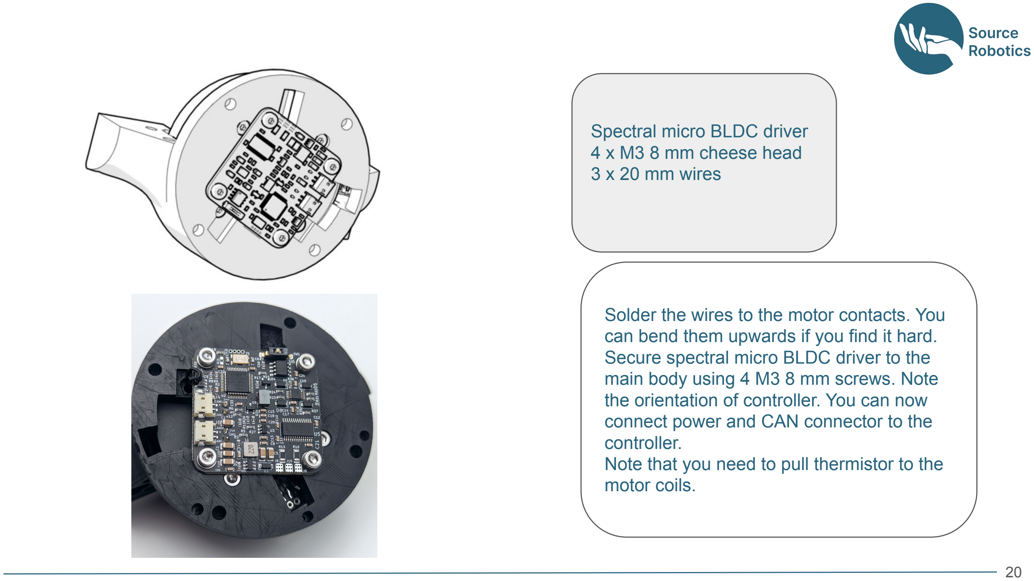
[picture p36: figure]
Spectral micro BLDC driver 4 x M3 8 mm cheese head 3 x 20 mm wires; main body using 4 M3 8 mm screws. Note; connect power and CAN connector to the controller.; motor coils.

Solder the wires to the motor contacts. You can bend them upwards if you find it hard. Secure spectral micro BLDC driver to the

the orientation of controller. You can now

Note that you need to pull thermistor to the

Position thermistor like shown in the image. Apply thermal cement to it and let it dry.

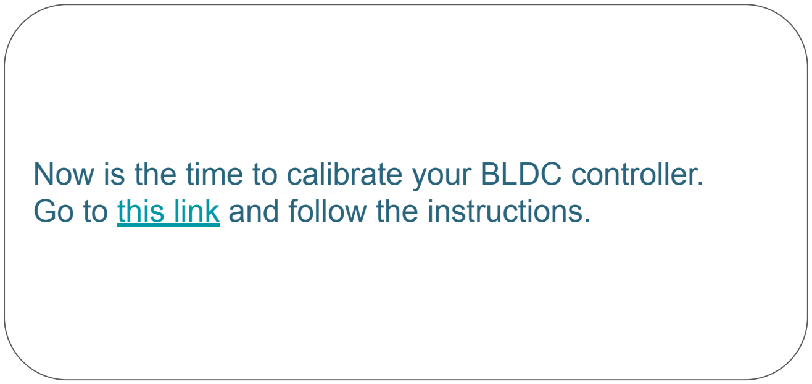
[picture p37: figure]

Now is the time to calibrate your BLDC controller. Go to this link (https://source-robotics.github.io/Spectral-BLDC-docs/apage4_calibration/) and follow the instructions.

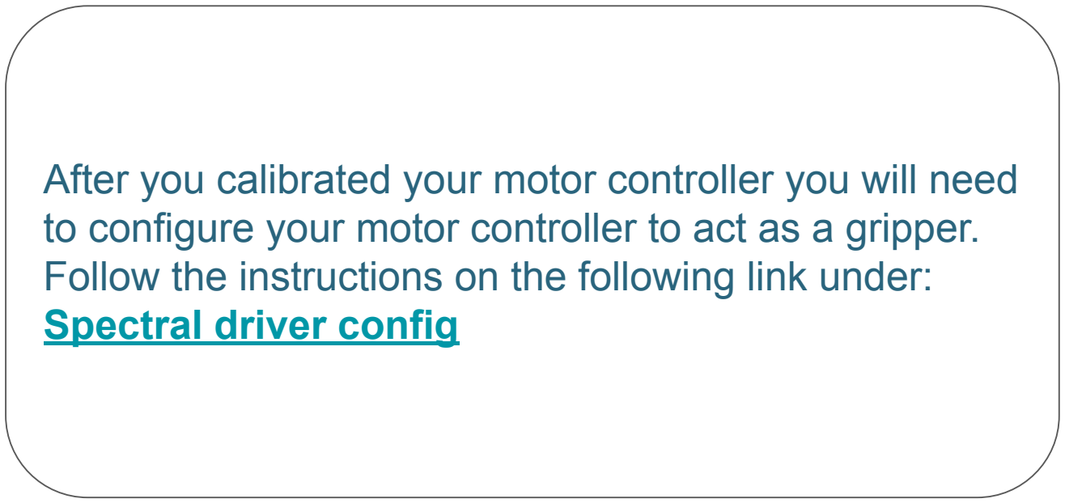
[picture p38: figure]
Spectral driver config

## After you calibrated your motor controller you will need

to configure your motor controller to act as a gripper.

## Follow the instructions on the following link under:

guide cover. Apply lithium grease to the

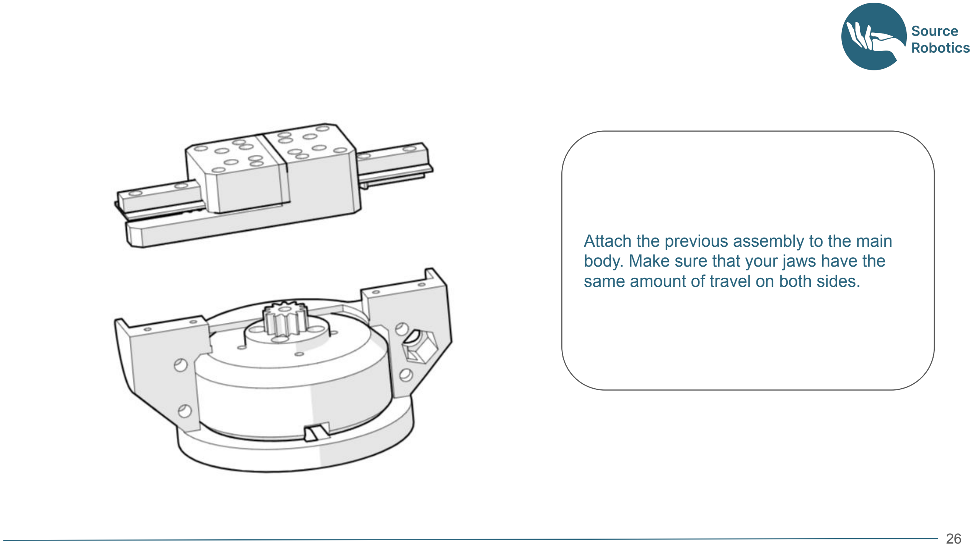
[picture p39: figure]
body. Make sure that your jaws have the same amount of travel on both sides.

Attach the previous assembly to the main

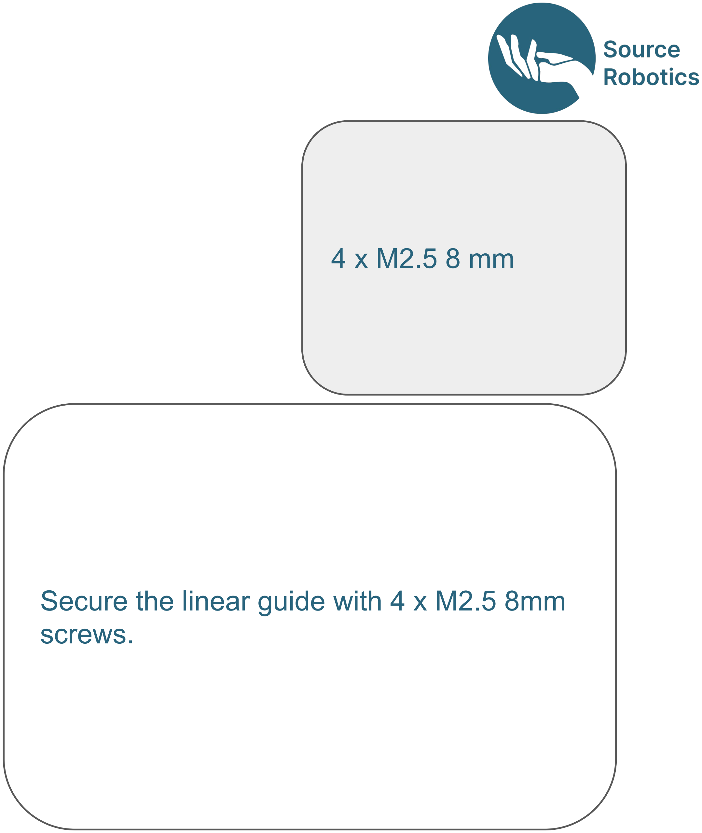
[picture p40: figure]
screws.

Secure the linear guide with 4 x M2.5 8mm

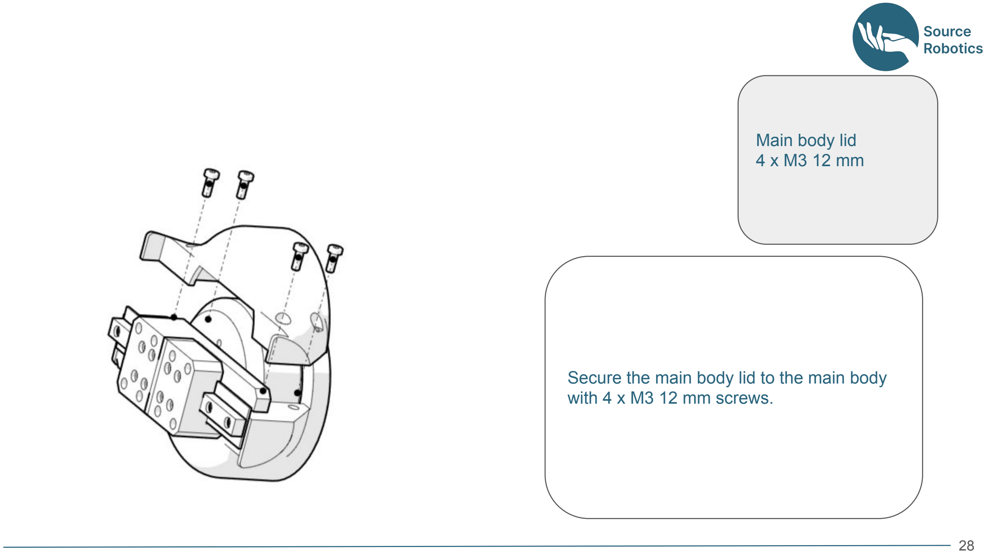
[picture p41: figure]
Main body lid 4 x M3 12 mm; with 4 x M3 12 mm screws.

Secure the main body lid to the main body

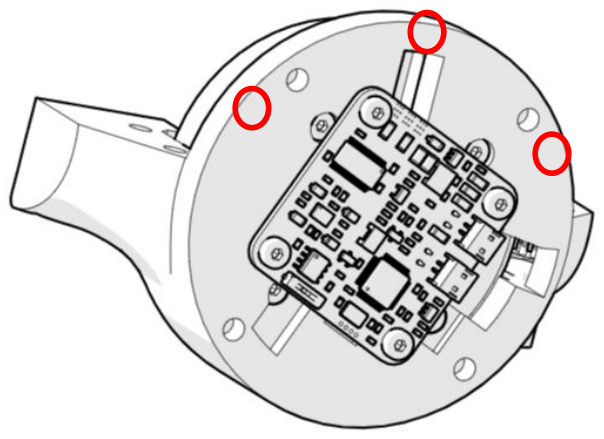
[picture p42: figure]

Optional step!
You will need to perform this step if there is large gap between two shells. Reasons for this can be a poor print quality of you parts. Secure Lid to main body with 3 M2 screws on the spots marked with red circles.

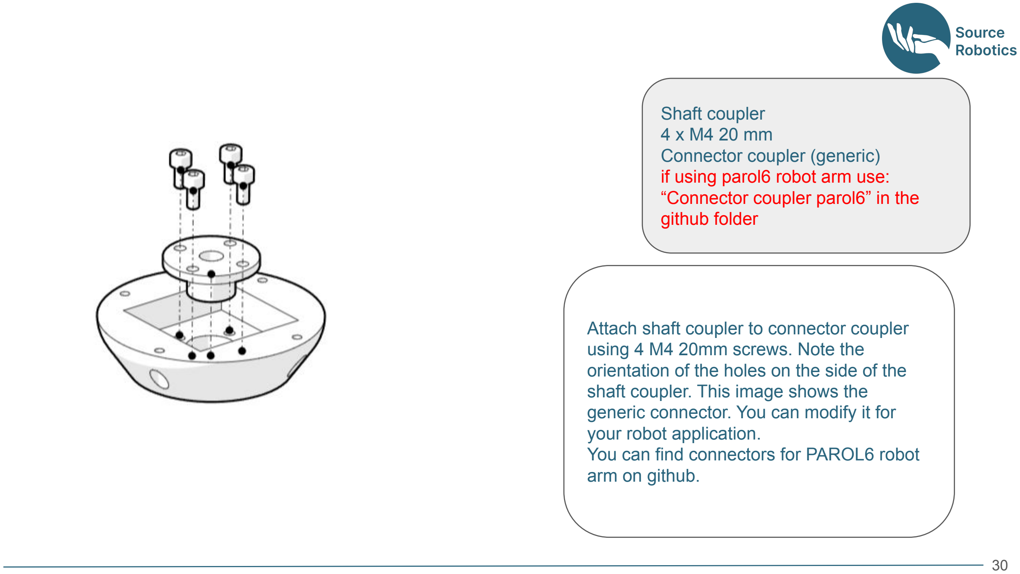
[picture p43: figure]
Shaft coupler 4 x M4 20 mm Connector coupler (generic) if using parol6 robot arm use: “Connector coupler parol6” in the github folder; using 4 M4 20mm screws. Note the; shaft coupler. This image shows the; your robot application.; arm on github.

Attach shaft coupler to connector coupler

orientation of the holes on the side of the

generic connector. You can modify it for

You can find connectors for PAROL6 robot

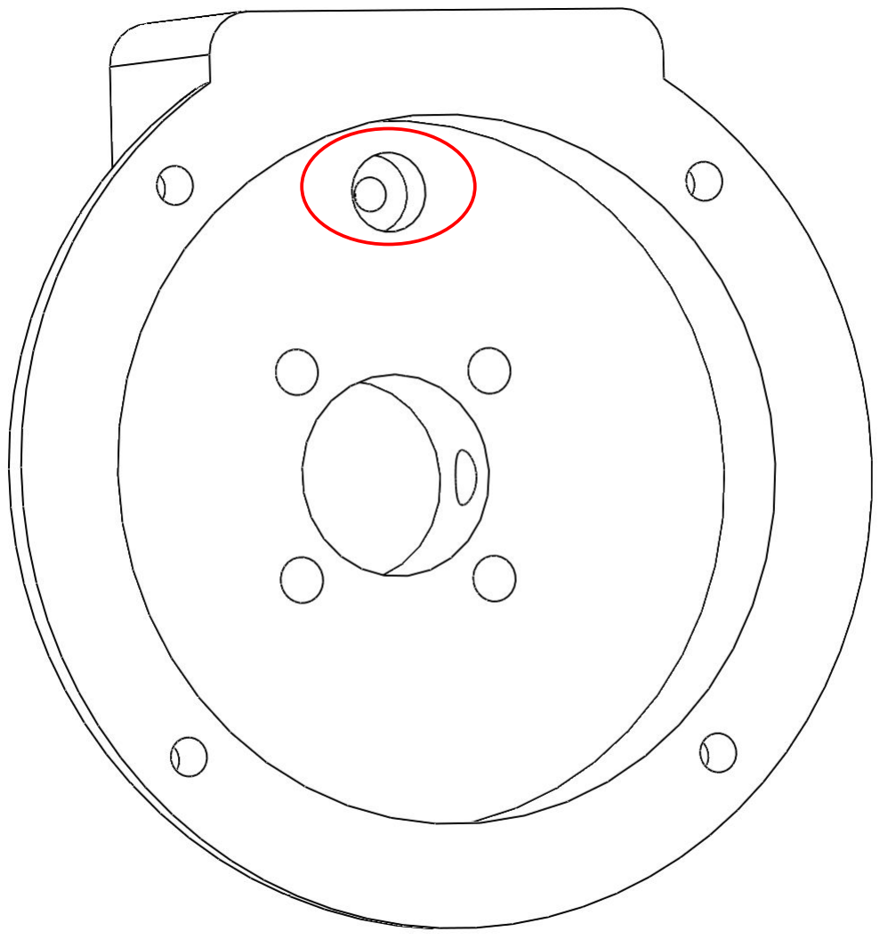
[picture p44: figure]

In case you are using the gripper with PAROL6 robot you will also need to use one M3 x 12mm screw and place it in the hole marked with circle. This will be used to home the robot.
*Note the part on the image is how “Connector coupler parol6” will look

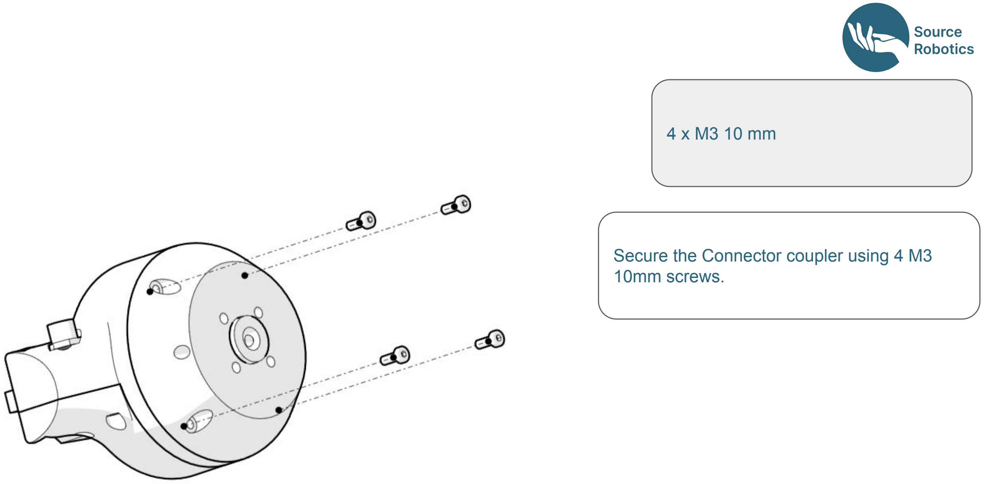
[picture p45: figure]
Secure the Connector coupler using 4 M3 10mm screws.

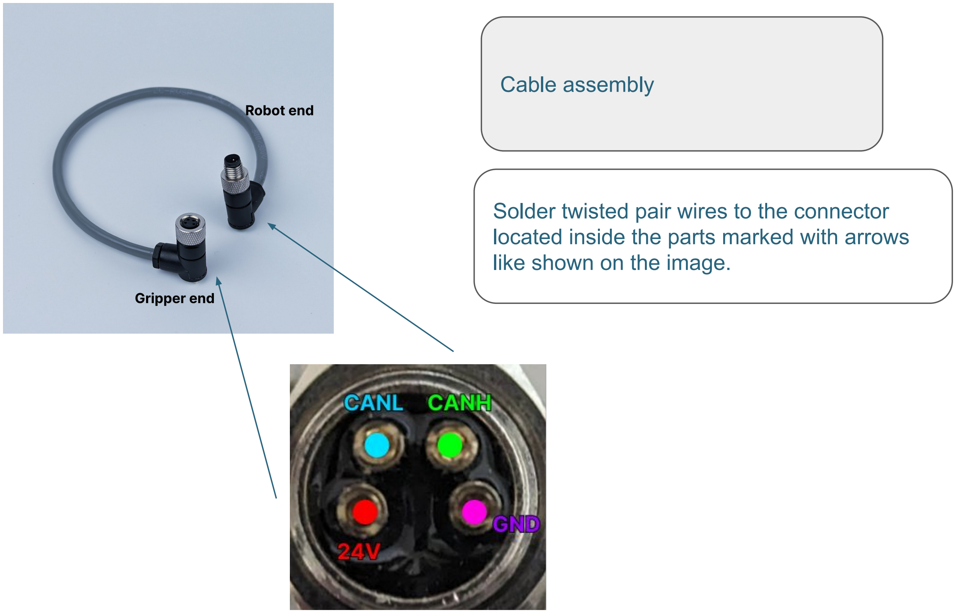
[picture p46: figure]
Cable assembly; like shown on the image.

Solder twisted pair wires to the connector located inside the parts marked with arrows

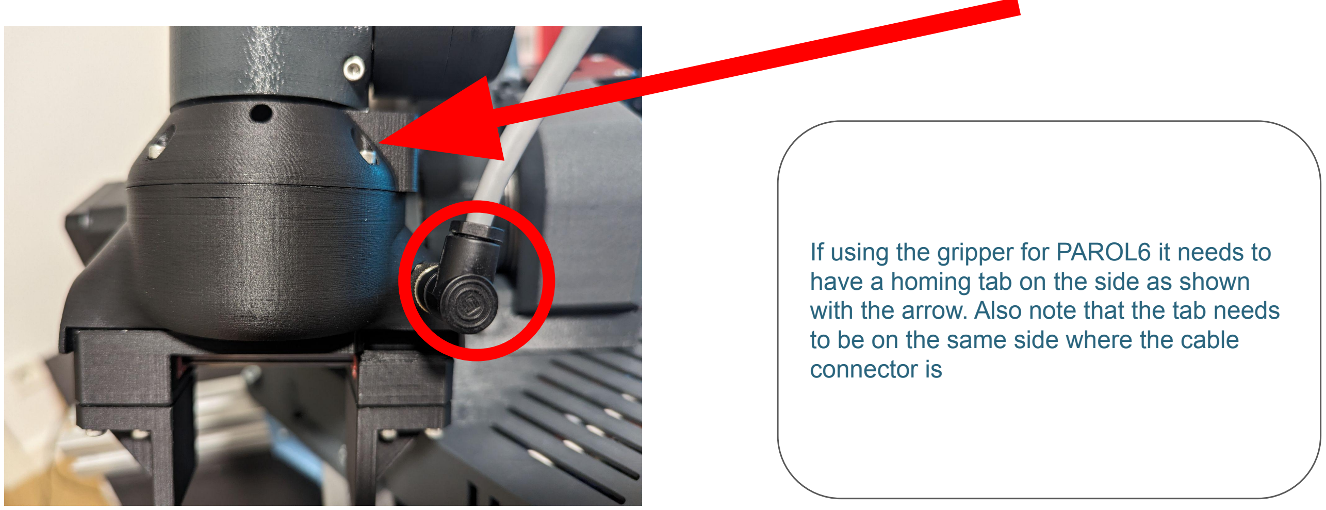
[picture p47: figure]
have a homing tab on the side as shown; to be on the same side where the cable connector is

If using the gripper for PAROL6 it needs to

with the arrow. Also note that the tab needs

# Congrats you are done!

Go to the docs to get your gripper up and running! (https://source-robotics.github.io/PAROL-docs/) https://source-robotics.github.io/SSG48-gripper-docs/page1_about_the_gripper/

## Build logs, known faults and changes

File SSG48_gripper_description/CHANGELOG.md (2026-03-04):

# Changelog – Source Robotics PAR6 Description

All notable changes to this model will be documented in this file.

## [10-2-2025]
- Added the initial files:
    - MJCF for PAR6 with SSG48 and MSG grippers
    - URDF files for 3 versions: PAR6 with flange, SSG48 gripper and MSG gripper
    - Added extra jaw options for SSG48 gripper

## [4-3-2025]
- From the initial release of PAR6 files we extracted:
    - URDF models of MSG and SSG48 gripper
    - MJCF models of MSG and SSG48 gripper

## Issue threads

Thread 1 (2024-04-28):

BOM link to BLDC Motor is 404

motivemachine, 2024-04-28:
The link for the motor from Aliexpress appears to be dead. Is there another source for the motor or a size/part # I missed in the docs somewhere?

PCrnjak, 2024-04-28:
It is updated now. Thank you for noticing it :D

PCrnjak, 2024-04-29:
Updated the link in the bom

Closed 2024-04-29.

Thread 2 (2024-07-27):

Link of 4 pin female wire connector is ambiguous

yoneken, 2024-07-27:
There are several options for 4pin female wire connector of [the current link](https://s.click.aliexpress.com/e/_DCG5Rff).
One is the screw type and another is the welding one.

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

The outer diameter of the screw type (φ14mm) is bigger than the welding one (φ12mm). And the outer diameter of the screw type interferes with the shell of gripper and does not fit!
We should choose the welding type.

PCrnjak, 2024-07-27:
Use welding type both for the cables and the gripper

yoneken, 2024-07-27:
I bought a screw one ;(

Closed 2024-09-01.

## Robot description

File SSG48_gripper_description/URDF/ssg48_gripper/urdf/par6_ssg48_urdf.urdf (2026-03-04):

<?xml version="1.0" encoding="utf-8"?>
<!-- SSG48 Gripper only  PAR6 robot arm links removed -->
<robot name="ssg48_gripper">
  <link name="gripper">
    <inertial>
      <origin xyz="-6.7987E-05 0.0001694 -0.077391" rpy="0 0 0" />
      <mass value="0.374" />
      <inertia ixx="0.00012751" ixy="-1.7736E-07" ixz="-2.8206E-06" iyy="5.8635E-05" iyz="-5.29E-07" izz="0.00014769" />
    </inertial>
    <visual>
      <origin xyz="0 0 0" rpy="0 0 0" />
      <geometry>
        <mesh filename="package://ssg48_gripper/meshes/gripper.STL" />
      </geometry>
      <material name="">
        <color rgba="0.792156862745098 0.819607843137255 0.933333333333333 1" />
      </material>
    </visual>
    <collision>
      <origin xyz="0 0 0" rpy="0 0 0" />
      <geometry>
        <mesh filename="package://ssg48_gripper/meshes/gripper.STL" />
      </geometry>
    </collision>
  </link>
  <link name="jaw1">
    <inertial>
      <origin xyz="0.0033269 0.029197 -0.0097237" rpy="0 0 0" />
      <mass value="0.02" />
      <inertia ixx="3.7875E-06" ixy="6.5971E-07" ixz="3.113E-07" iyy="1.5397E-06" iyz="-6.1777E-07" izz="4.4716E-06" />
    </inertial>
    <visual>
      <origin xyz="0 0 0" rpy="0 0 0" />
      <geometry>
        <mesh filename="package://ssg48_gripper/meshes/jaw1.STL" />
      </geometry>
      <material name="">
        <color rgba="0.29804 0.29804 0.29804 1" />
      </material>
    </visual>
    <collision>
      <origin xyz="0 0 0" rpy="0 0 0" />
      <geometry>
        <mesh filename="package://ssg48_gripper/meshes/jaw1.STL" />
      </geometry>
    </collision>
  </link>
  <joint name="jaw1_JOINT" type="prismatic">
    <origin xyz="0 0 -0.11745" rpy="-3.1416 0 -3.1416" />
    <parent link="gripper" />
    <child link="jaw1" />
    <axis xyz="0 -1 0" />
    <limit lower="-0.024" upper="0" effort="20" velocity="0.1" />
  </joint>
  <link name="jaw2">
    <inertial>
      <origin xyz="-0.0033269 -0.029197 -0.0097237" rpy="0 0 0" />
      <mass value="0.02" />
      <inertia ixx="3.7875E-06" ixy="6.5971E-07" ixz="-3.113E-07" iyy="1.5397E-06" iyz="6.1777E-07" izz="4.4716E-06" />
    </inertial>
    <visual>
      <origin xyz="0 0 0" rpy="0 0 0" />
      <geometry>
        <mesh filename="package://ssg48_gripper/meshes/jaw2.STL" />
      </geometry>
      <material name="">
        <color rgba="0.29804 0.29804 0.29804 1" />
      </material>
    </visual>
    <collision>
      <origin xyz="0 0 0" rpy="0 0 0" />
      <geometry>
        <mesh filename="package://ssg48_gripper/meshes/jaw2.STL" />
      </geometry>
    </collision>
  </link>
  <joint name="jaw2_JOINT" type="prismatic">
    <mimic joint="jaw1_JOINT" multiplier="-1" offset="0"/>
    <origin xyz="0 0 -0.11745" rpy="-3.1416 0 -3.1416" />
    <parent link="gripper" />
    <child link="jaw2" />
    <axis xyz="0 -1 0" />
    <limit lower="0" upper="0.024" effort="20" velocity="0.1" />
  </joint>

  <link name="tcp">
    <visual>
      <origin xyz="0 0 0" rpy="0 0 0"/>
      <geometry>
        <sphere radius="0.003"/>
      </geometry>
      <material name="red">
        <color rgba="1 0 0 1"/>
      </material>
    </visual>
  </link>

  <joint name="tcp_fixed_joint" type="fixed">
    <parent link="gripper"/>
    <child link="tcp"/>
    <origin xyz="0 0 -0.16" rpy="0 0 0"/>
  </joint>

  <transmission name="jaw_transmission">
    <type>transmission_interface/SimpleTransmission</type>
    <joint name="jaw1_JOINT">
      <hardwareInterface>PositionJointInterface</hardwareInterface>
    </joint>
    <actuator name="jaw_motor">
      <hardwareInterface>PositionJointInterface</hardwareInterface>
      <mechanicalReduction>1</mechanicalReduction>
    </actuator>
  </transmission>

</robot>

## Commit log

2024-03-16 Added BOM an assembly manual
    [Gripper_BOM.xlsx]
2024-03-16 Added STL files and STEPS
    [Guide_cover.STL, Jaw.STL, Jaw_plate.STEP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]
2024-03-18 update stl files
    [Jaw.STL]
2024-03-26 update bom linear rail
    [Gripper_BOM.xlsx]
2024-03-26 updated assembly manual
2024-03-28 UPDATE on coupler for PAROL6
2024-03-30 Update Gripper_assembly manual.pdf
2024-04-02 add step files
    [JAW.STEP]
2024-04-28 bom update
    [Gripper_BOM.xlsx]
2024-04-30 added generic fingers
    [Finger_1.STL]
2024-05-28 small update to the assembly manual
2024-06-20 update bom
    [Gripper BOM.xlsx, Gripper_BOM.xlsx]
2024-11-26 update to BOM
    [Gripper BOM.xlsx]
2024-12-22 added TPU fin ray jaws files
    [Jaw_plate_fin_ray.STEP, Jaw_plate_fin_ray.STL, fin_ray_1.STEP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]
2025-01-20 Added steps
    [Guide_Cover.STEP, Lid.STEP, Magnet_shaft.STEP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]
2025-03-03 updated gripper folder name
    [Guide_Cover.STEP, Lid.STEP, Magnet_shaft.STEP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]
2025-04-11 update to STL files
    [Finger_1.STL, Jaw_plate_fin_ray.STEP, Jaw_plate_fin_ray.STL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]
2025-05-22 added gripper jaw
    [gripper_jaw.STL]
2025-08-10 updated BOM
2025-11-15 updated mainbody with larger blocker
    [solid_jaws_pinch_foam.STEP]
2026-02-19 Added building cables document
2026-02-27 update STL
2026-02-28 add secondary model for larger bldc motor
    [gripper_gear_large_bearing_motor.STL, magnet_shaft_large_bearing.STL]
2026-03-04 Added URDF & MJCF models
    [gripper.STL, gripper_SSG48.STL, jaw1.STL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]
2026-04-02 STEPO file update
    Updated STEP files for versions with large bldc motor
    [Gripper_mirror_body.STEP, UR_coupler_gripper.STEP, mainbody_large_bearing_version.STEP]
2026-04-17 Add motor datasheet

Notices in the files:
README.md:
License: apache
